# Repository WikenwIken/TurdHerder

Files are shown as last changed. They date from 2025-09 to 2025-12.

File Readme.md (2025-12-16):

# Turd Herder 
## _The Porcelain Standard for 3D Printer Waste Management_
### THIS PROJECT IS A WORK IN PROGRESS.
If you would like to help with the development of this project please join us in the  [Armored Turtle Discord Thread].  The files contained in this github are usable, however unreliable in their current state.

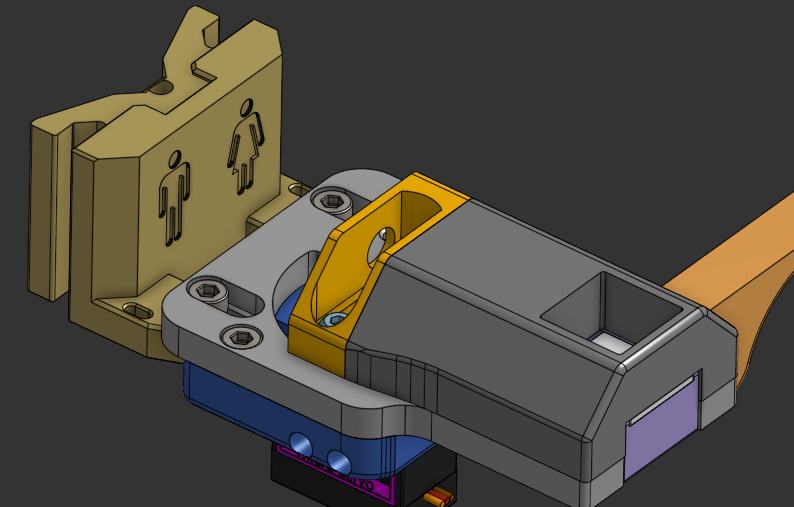
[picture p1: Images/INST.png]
INST


The Turd Herder is a dookie disposal system for 3D printers with toolheads that have limited to no travel past the edges of the print bed.  The bowl extends over the edge of the print bed, receives the "payload," retracts and whisks it off to a tank in the depths below.  

Turd Herder was designed for use with the Voron Trident / Box Turtle AMS combo running Klipper firmware. The macros are designed to integrate with the AFC Macros (included with the Box Turtle system).

The motion system was inspired by [Dendrowen's Blobifier], the mounting system incorporates whole, and modified, parts from [Armored Turtle's AT Brush]  and the macros are modified versions of [ImSundee's Turtleblobifier].

### 2025.11.20 - Added __front_arm_base_extended.stl__ to the 20255.11.01 STL folder and added the corresponding STEP files in an accurate, yet confusingly named folder. 
#### 2025.11.01 - Updated the mounting location of the switch for better reliability and stability.  Only __Cog__, __Slide_Base__ and __Servo_Mount__ have changed since last version. 
##### 2025.09.03 - This project is brand new and only tested by the me so far.  Bugs / hitches are to be expected.  Please report anything that isn't working as expected and it will be addressed. 

## Features

- Can be used with any toolhead / probe combo as there aren't any negative Z moves
- A modified G28 allows for safe Z homing 
- Easy to print parts, no supports required!
- Plugs into a BL Touch Port for easy wiring
- Optional brush attachment creates an all-in-one solution

## Required Tools
- Sodering Iron
- Crimping Tool
- Wire Stripper
- Allen Wrenches / Hex Drivers (1.5, 2, 2.5 and 3 mm)
- Small Phillips Screw Driver

## BOM

| Part | QTY | 
| --- | --- |
| MG90S Servo (180°) + Hardware Kit | 1 |
| Micro Limit Switch (with lever) | 1 |
| Bambu A1 style brush (37x8) | 1 |
| 6 x 3 mm magnet | 2 |
| 15 x 14 x 1 mm aluminum cube | 1 |
| M5 x 10 mm SHCS | 2 |
| M5 Rollnut | 2 |
| M3 Hex Nut | 2 |
| M3 Washer | 1 |
| M3 x 5 x 4 mm Heat Set Insert | 8 |
| M3 x 6 mm SHCS | 2 | 
| M3 x 8 mm SHCS | 4 |
| M3 x 8 mm BHCS | 1 |
| M3 x 6 mm BHCS | 1 |
| M2 x 8 mm SHCS | 2 |
| 3 mm ID Bowden Tube (optional) | ~4.5 mm |
| JST-XH Male / Female Plugs / Crimps | ~ |
| Zip Ties (optional) | ~ |

*Note:  the M3 Hex Nuts MUST be magnetic.  The sled mechanism will not work properly without a strong-ish magnetic connection.*

*Note: The aluminum cube is just a landing pad for the ___hot___ load and can be made of anything that will take the heat better than bare plastic.  We don't want things to stick and get clogged.  I cut up an aluminum plate from an old project box but as long as its <=1mm thick you could fold up some aluminum foil or glue a few layers of soda cans together.  Get creative.*

## Printing

In addition to the STLs in this repositiory, Turd Herder requires the following parts from the [AFC-Accessories] repo.
- [mount_lower.stl]
- [mount_upper.stl]

Parts should be printed in ABS and in accordance to typical Voron specs which may be found [here]. Tolerances for the slots are a little tight and may require some filing to achieve a smooth translation from front to rear.
All parts are oriented correctly and don't require any modifiers from the slicer.  
Supports should not be needed.

# Software Installation
__It is important that the software be installed prior to building the Turd Herder as some of the macros are vital to the assembly process.__

__It is recommended that you make a backup of your __printer.cfg__ and __/AFC/AFC.cfg__ files before proceeding.__

Variables do not need to be tuned at this point, we're just installing the software so the servo macros may be utilized for the build.  We will cover the critical variables later in this document.

1) Clone this project into your printer's config folder ``` git clone https://github.com/WikenwIken/TurdHerder ~/printer_data/config/TurdHerder ```
2) Open TurdHerder/turd_hw.cfg and set the correct values for `pin` and `switch_pin`  
3) Make the following changes to your printer.cfg file:
    - Add ```[include TurdHerder/turdherder.cfg]```
    - Paste the sections `[force_move]` and `[homing_override]` from /turdherder/printurd.cfg into your printer.cfg, adding in any custom features that were previously executed in `[safe_z_home]`
    - Comment out ```[safe_z_home]``` and all lines included within.  This seems crazy but '[homing_override]' and '[safe_z_home]' are incompatable.  
4) Make the adjustments to your /AFC/AFC.cfg file as noted in the second half of the /TurdHerder/printurd.cfg file

# Assembly

1) Install 6 M3 heat set inserts according to Figures 1 and 2: 
    - front_arm_base x2 
    - servo_base x2 
    - chimney x2

Fig. 1    
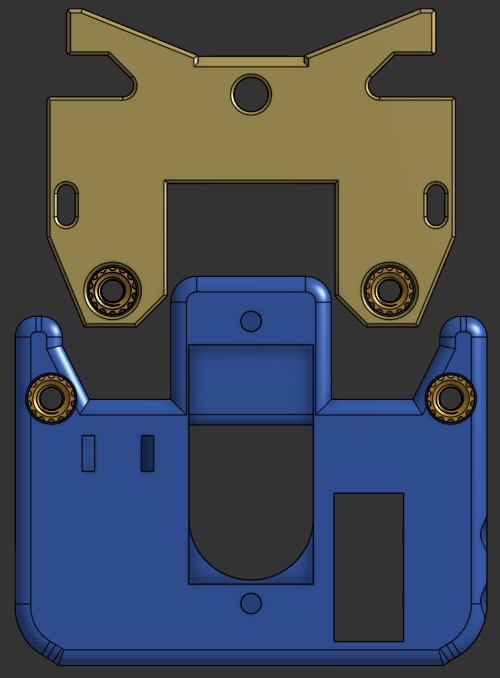
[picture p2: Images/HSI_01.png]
HSI_01


Fig. 2
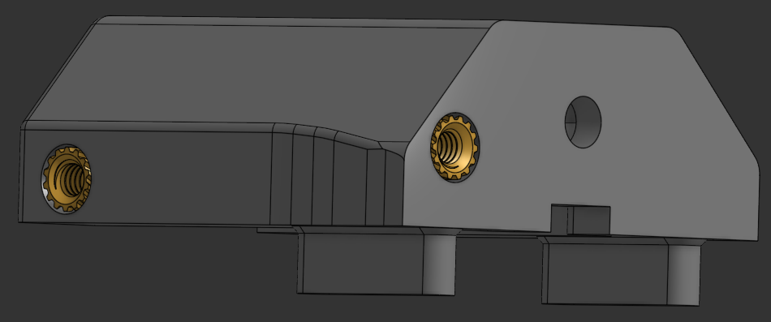
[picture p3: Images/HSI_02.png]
HSI_02


2) Install 2 M3 heat set inserts into __mount_upper__ according to [Step 4] of the AT Brush Manual.
3) Solder one wire to each of the outer pins of the micro limit switch.  Terminate each wire with an appropriate sized crimp / plug.  Orientation in the plug does not matter for the limit switch.
4) MG90S Servos typically ship with dupont connectors.  These will need to be removed and replaced by an appropriate connector.  Consult your main board's pinout diagram before building your new connector.
5) Attach the servo to the __servo_mount__ using the self-tapping screws that came with the servo.  It will only fit one way.
6) Secure the __slide_base__ to the __servo_mount__ using 2 M3x8 SHCS (Figure 3)
7) Plug the servo into the socket on the main board that you defined in /TurdHerder/turd_hw.cfg.  
    - Execute the macro ```SERVO_IN```.  This should rotate the shaft *clockwise*  
    - Execute the macro ```SERVO_OUT```.  This should rotate the shaft *counter-clockwise*
    - If the shaft does not rotate, check your wiring / pin definitions.
    - If the shaft rotates in the wrong direction some modification of the code is likely in order to make it work with your motor.
8) _Make absolutely sure, before proceeding, that your printer homes as expected without the Turd Herder in place._  Run the 'servo_out' macro.  Z should increase and the servo should move after.  Homing the printer should home X and Y first, retract the servo and then move to the "safe" spot and then home Z.
9) Execute the macro ```SERVO_OUT``` and press the __cog__ onto the shaft as seen in Figure 3.  Add the M3 Washer and M2.5 mounting screw if the __cog__ isn't as rigid as you would prefer.  It should be a pretty tight fit.  Once installed, execute the macros ```SERVO_IN``` and ```SERVO_OUT``` to confirm the cog has full range of travel.  
*Note: The motor should complete its move without physically butting up against the frame.  If the motor doesn't stop freely then some physical / code adjustments should be made.*

Fig. 3

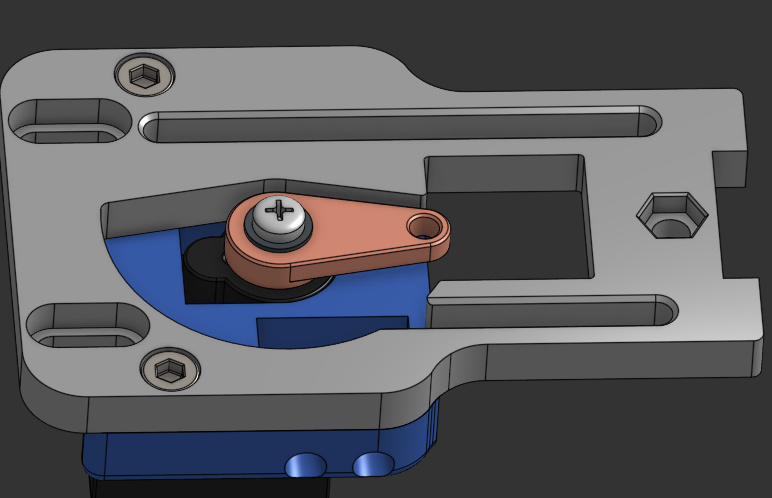
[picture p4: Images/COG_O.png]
COG_O


10) Ensure that the cog is in the position indicated in Figure 3 by running the ```SERVO_OUT``` macro and unplug the servo from the main board before moving on.
11) Feed the limit switch up through the rectangular hole in the __servo_mount__ and secure it in place with M2x8 screws.  __Mind the orientation in Figure 4.__

Fig. 4

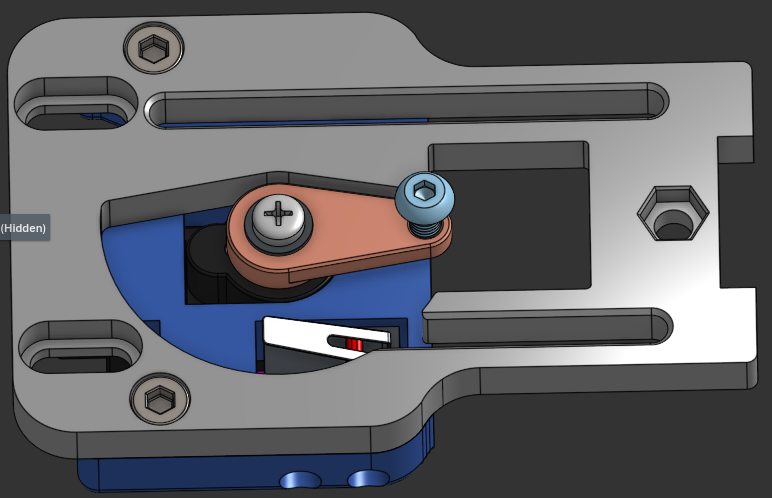
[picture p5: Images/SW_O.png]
SW


12) Insert 1 M3 Hex Nut into the cutout in the __slide_mount__.  If the fit is too tight to press in with your fingers it may be useful to "pull" it into place with an M3 screw from the bottom of the part.  If the fit is too loose use a dab of super glue or insert an M3x4 or M3x5 screw from below that won't protrude above the nut to hold it in place.  
13) Insert 2 6 x 3 mm magnets into the holes in __sled__.  A dab of super glue may be required to old them in place.  Polarity is not important.  Be careful not to split the layers.    
14) Glue the Aluminum Plate onto the tray of the __sled__.  It should not protrude above the edges of the tray.
15) Click the __sled__ in place on the __slide_mount__ (Figure 5)

Fig. 5

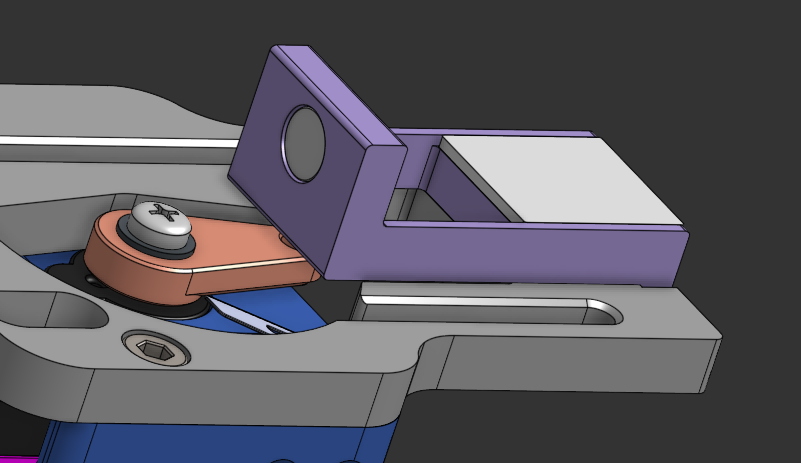
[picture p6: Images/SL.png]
SL


16) Attach the __chimney_slot__ to the __chimney__ by inserting an M3x6 SHCS into the hole on the left-rear of the parts. (Figure 6)
17) Insert 1 M3 Hex Nut into the cutout in the __chimney__ and secure it with an M3x6 BHCS through the holes in the middle. (Figure 7)

Fig. 6

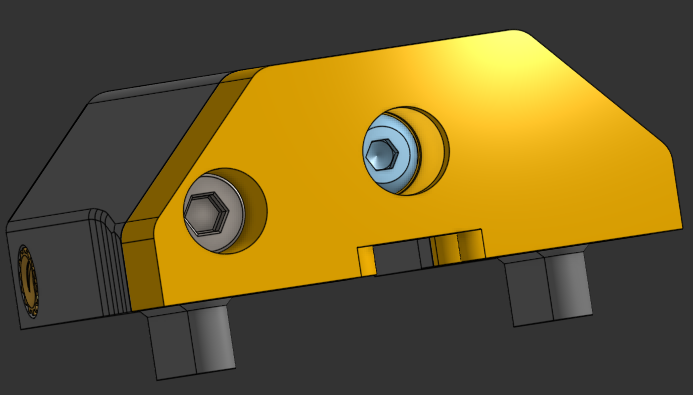
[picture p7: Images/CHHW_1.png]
CHHW_1


Fig. 7

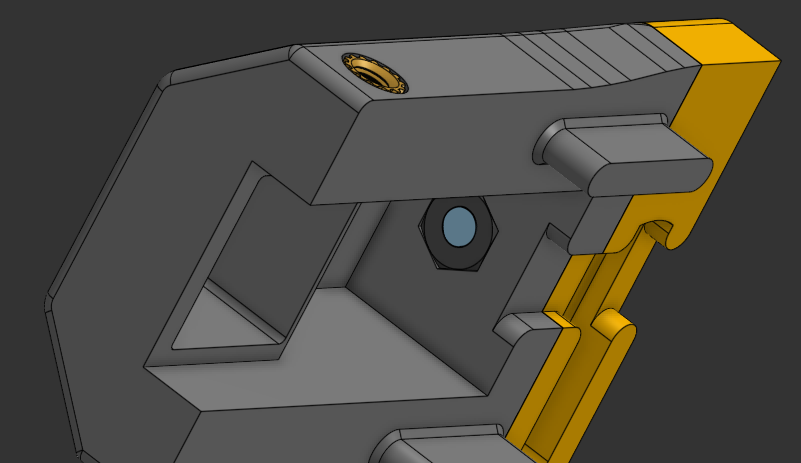
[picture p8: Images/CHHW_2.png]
CHWW_2


18) Drop the chimney assembly into the slots on the __slide_mount__.  The top of the __sled__ inserts into the space in the __chimney__ with the M3 Hex Nut.  Align the slot in the __chimney_slot__ with the hole in the slender end of the __cog__ and screw an M3x8 BHCS into the __cog__ until it is flush with the underside (Figure 8).  It should not protrude from the bottom at all.  This connection should remain fairly loose to allow for free translation of the screw in the slot.  It is easily adjusted later if movement is labored.
_OPTIONAL: A 4mm OD x 3mm ID bowden tube sleeve may be installed around the M3x8 screw to cut down on the threads wearing out the slot_

Fig. 8

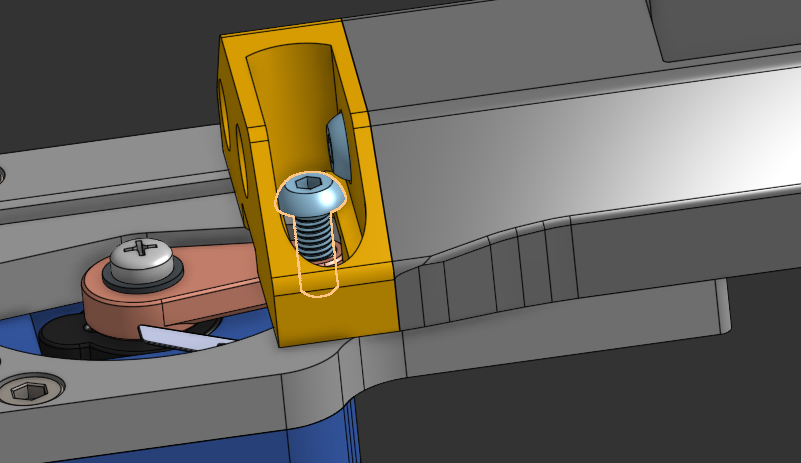
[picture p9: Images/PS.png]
PS


19) Attach the __brush_arm__ to the __chimney__ using an M3x6 SHCS (Figure 9).

Fig. 9

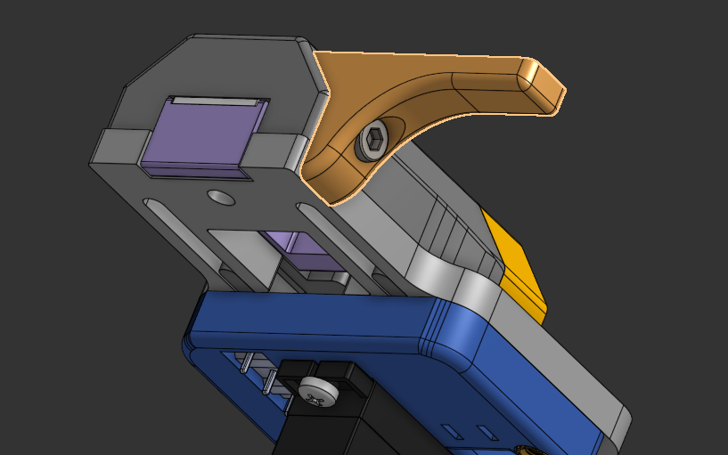
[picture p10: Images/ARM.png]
ARM


20) Attach the silicone brush to the top surface of the __brush_arm__ 
21) Assembly of the Turd Herder is complete.  (Figure 9)

22) Follow these instructions in the [AT Brush Manual] utilizing the modified __front_arm_base__ from this repository:
    - Steps 1 - 8
    - Steps 13 - 15
23) Loosely attach the Turd Herder assembly to the frame mount assembly using 2 M3x8 SHCS (Figure 9).  Adjust the Y positioning so that there is ~1-2mm gap between the front of the Turd Herder and the print bed and tighten the screws.

Fig. 9

INST

24) Adjust the height of the assembly so that, when the Turd Herder is extended, the nozzle comes in contact with the brush on the Z axis.  (See Step 16 in the [AT Brush Manual])

25) Plug the servo and the limit switch into the main board.  
    - Ensure smooth movement by cycling through the `SERVO_IN`, `SERVO_MID` and `SERVO_OUT` macros
    - Ensure the `turdherd` limit switch reads *detected* in the `SERVO_IN` and `SERVO_MID` positions.
    - Ensure the `turdherd` limit switch reads *not detected* in the `SERVO_OUT` position.
26) Congratulations!  The Turd Herder is fully assembled and the mechanism is working as intended!  Don't release those bowels just yet, there are a few more things to set up.

# Critical Variables
The following are the _must have_ variables that need to be defined for the specific printer that Turd Herder is being installed in.  Each variable is accompanied with a description within the .cfg file.
## turd_hw.cfg 
`[servo TURDHERDER]`
* `pin`

`[filament_switch_sensor turdherd]`
* `switch_pin`

## turdherder.cfg
`[gcode_macro TURDHERDER]`
* `variable_purge_spd`
* `variable_thbottom`
* `variable_brush_start_x`
* `variable_brush_start_y`
* `variable_purge_x`
* `variable_purge_y`
* `variable_tray_angle_mid`

## printer.cfg / printurd.cfg
`[homing_override]`
* `home_pos_x`
* `home_pos_y`

   [Dendrowen's Blobifier]: <https://github.com/Dendrowen/Blobifier>
   [ImSundee's Turtleblobifier]: https://github.com/ImSundee/Turtleblobifier
   [Armored Turtle's AT Brush]: https://github.com/ArmoredTurtle/AFC-Accessories/tree/main/AT_Brush
   [AFC-Accessories]: https://github.com/ArmoredTurtle/AFC-Accessories
   [mount_lower.stl]: https://github.com/ArmoredTurtle/AFC-Accessories/blob/main/AT_Brush/STLs/mount_lower.stl
   [mount_upper.stl]: https://github.com/ArmoredTurtle/AFC-Accessories/blob/main/AT_Brush/STLs/mount_upper.stl
   [here]:<https://docs.vorondesign.com/sourcing.html#print-settings>
   [AT Brush Manual]: https://www.armoredturtle.xyz/manual.html?manual=at_brush&step=1
   [Step 4]: https://www.armoredturtle.xyz/manual.html?manual=at_brush&step=4
   [Armored Turtle Discord Thread]: https://discordapp.com/channels/1229586267671629945/1413552213695008869

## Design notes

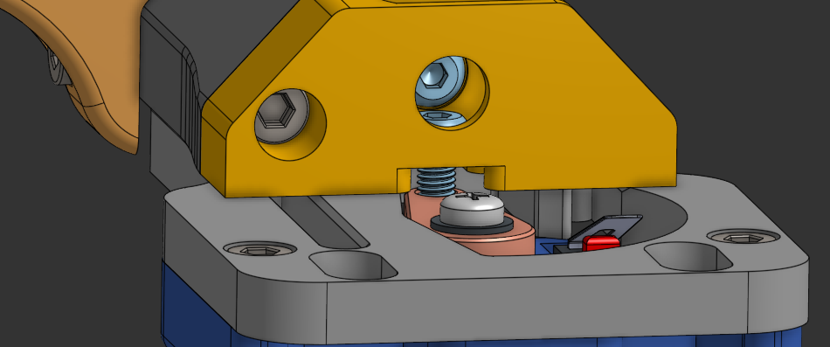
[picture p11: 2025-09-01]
Images/Hardware.png

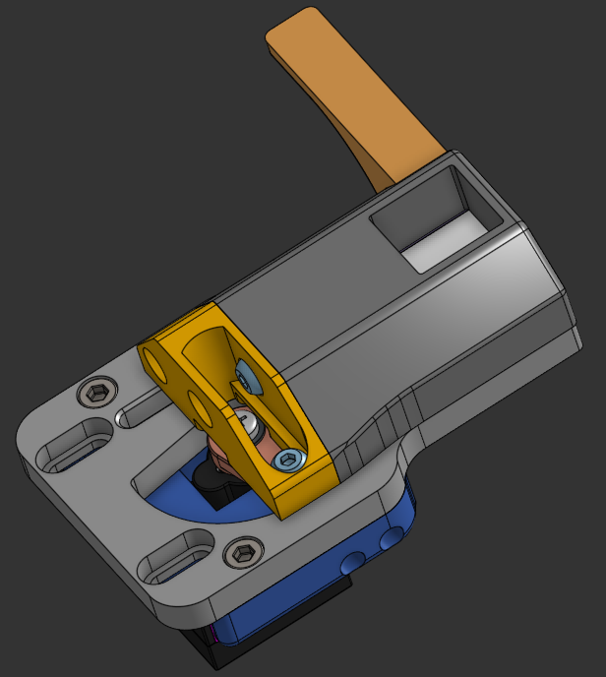
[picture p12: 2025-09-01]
Images/FINAL.png

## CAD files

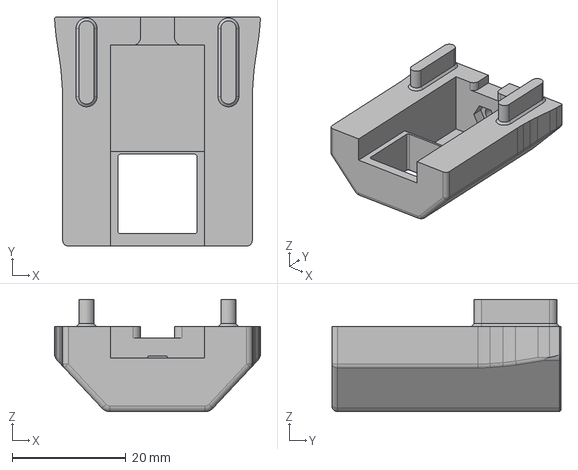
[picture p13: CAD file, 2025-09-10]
2025.09.09.Turd Herder_STEP/Chimney.step
36.3 x 40.4 x 19.8 mm

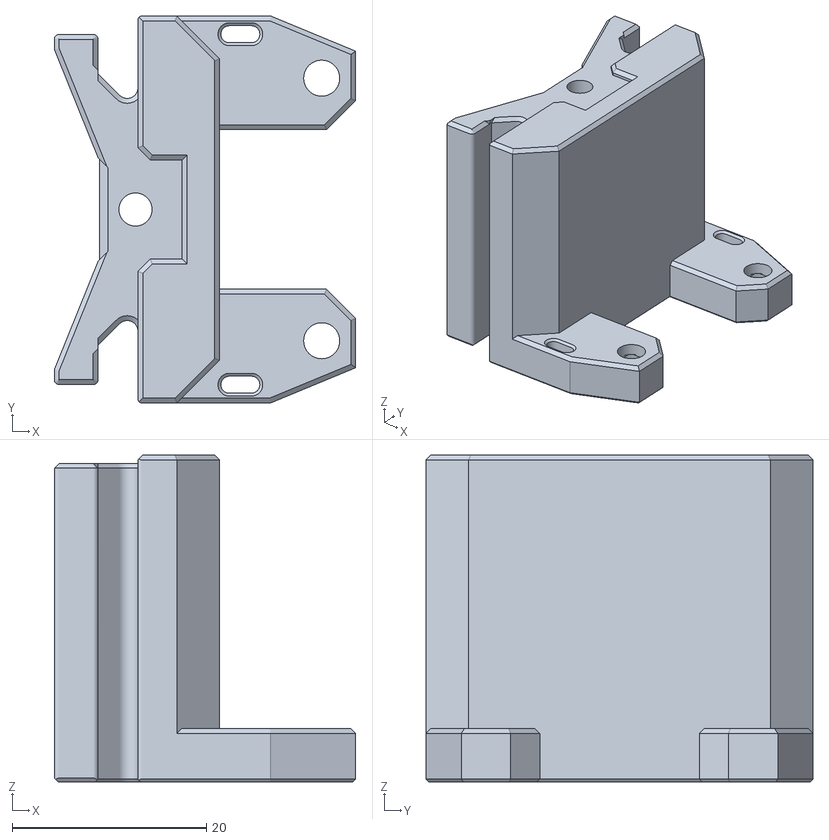
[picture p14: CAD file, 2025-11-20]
2025.11.01_Turd_Herder_STL/front_arm_base_taller.stl
31.0 x 39.8 x 33.6

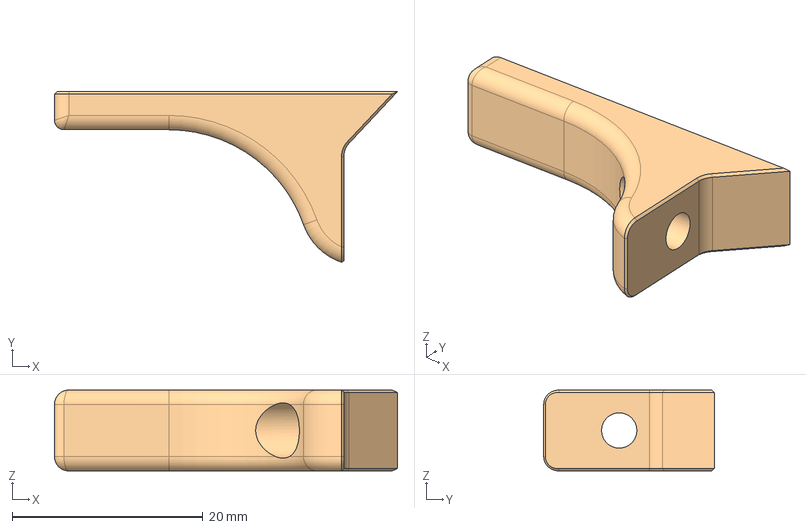
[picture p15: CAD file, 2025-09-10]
2025.09.09.Turd Herder_STEP/Brush_Arm.step
36.0 x 17.9 x 8.50 mm

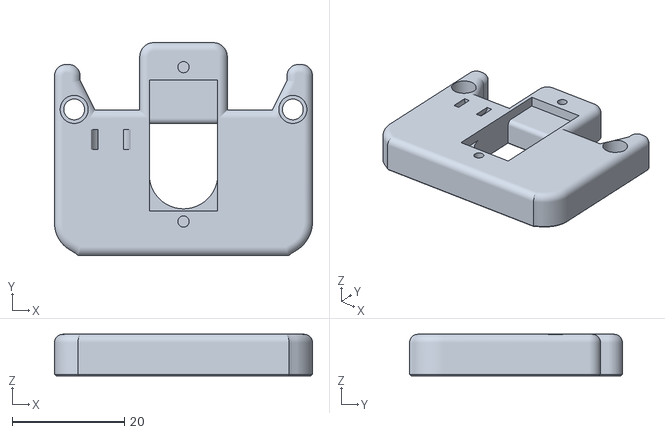
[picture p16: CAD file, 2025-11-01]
2025.11.01_Turd_Herder_STL/Servo_Mount.stl
46.0 x 37.9 x 7.40

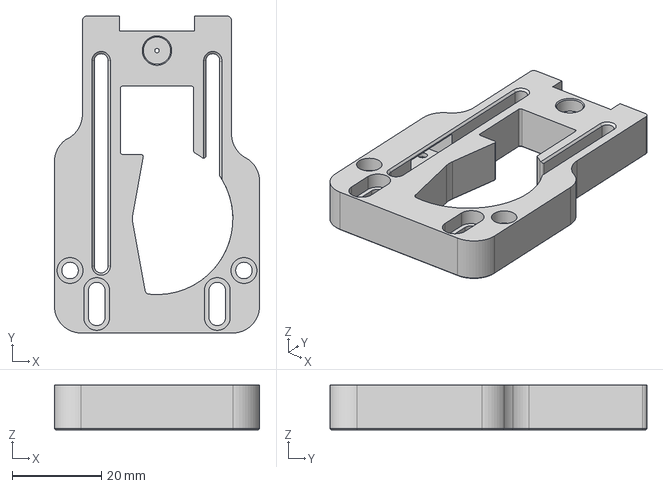
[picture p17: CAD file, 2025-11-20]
2025.11.20_Side_Switch_Parts_STEP/Side_Switch - Slide_Base.step
45.9 x 71.0 x 10.0 mm

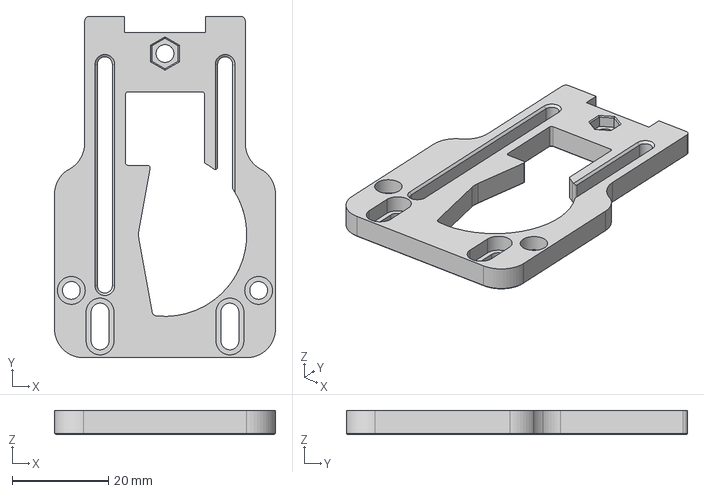
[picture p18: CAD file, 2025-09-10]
2025.09.09.Turd Herder_STEP/Slide_Base.step
45.9 x 71.0 x 5.00 mm

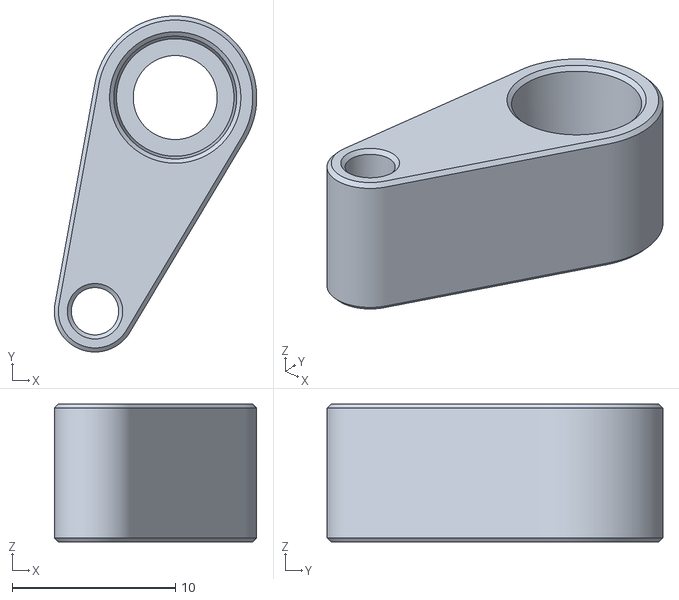
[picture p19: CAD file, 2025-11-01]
2025.11.01_Turd_Herder_STL/Cog.stl
12.4 x 20.6 x 8.45

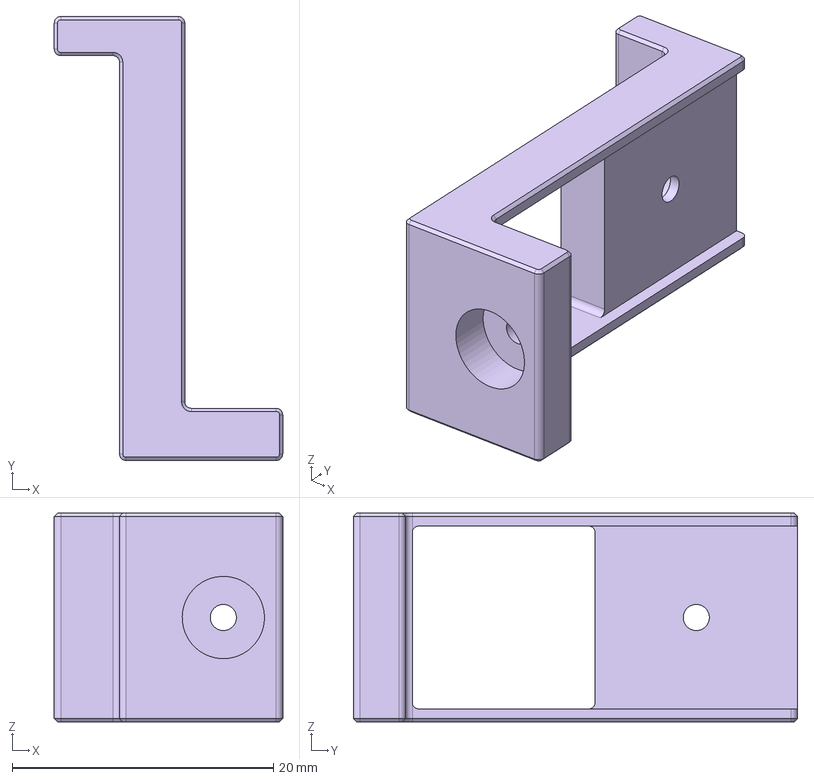
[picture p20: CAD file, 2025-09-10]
2025.09.09.Turd Herder_STEP/Sled.step
17.5 x 34.0 x 16.0 mm

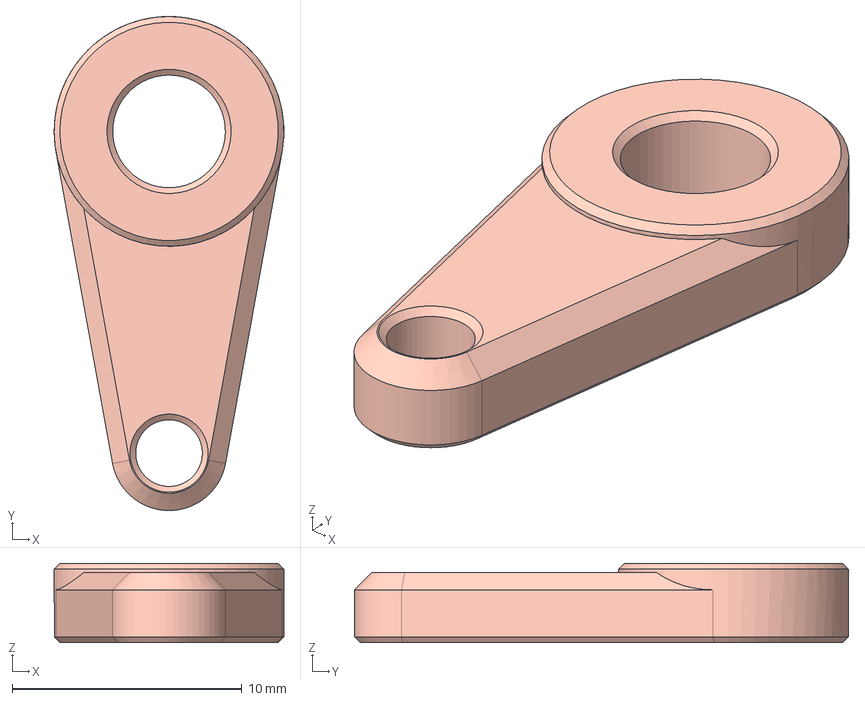
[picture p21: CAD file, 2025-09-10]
2025.09.09.Turd Herder_STEP/Cog.step
9.99 x 21.5 x 3.45 mm

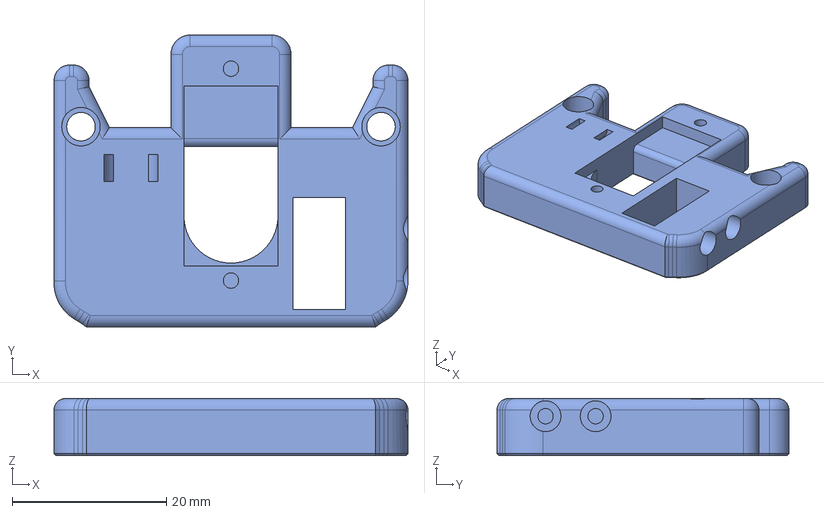
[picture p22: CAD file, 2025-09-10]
2025.09.09.Turd Herder_STEP/Servo_Mount.step
45.9 x 37.9 x 7.40 mm

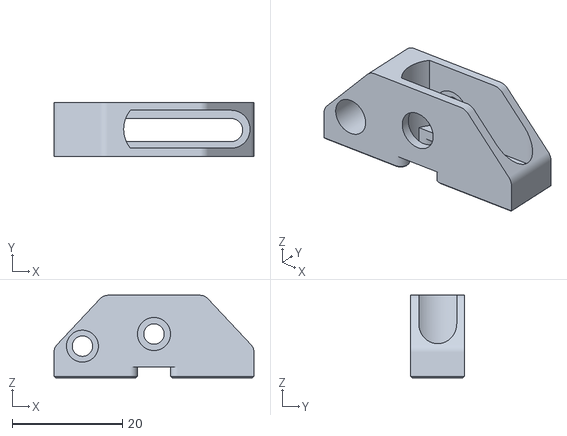
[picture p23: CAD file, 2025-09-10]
2025.11.01_Turd_Herder_STL/Chimney_Slot.stl
36.3 x 9.80 x 15.0

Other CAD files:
2025.11.20_Side_Switch_Parts_STEP/front_arm_base_taller.step
2025.11.20_Side_Switch_Parts_STEP/Side_Switch - Cog.step
2025.11.01_Turd_Herder_STL/Slide_Base.stl
2025.11.20_Side_Switch_Parts_STEP/Side_Switch - Servo_Mount.step
2025.11.01_Turd_Herder_STL/Chimney.stl
2025.09.09.Turd Herder_STEP/Chimney_Slot.step
2025.11.01_Turd_Herder_STL/Brush_Arm.stl
2025.09.09.Turd Herder_STEP/Front_Arm_Base.step
2025.09.09.Turd Herder_STL/Front_Arm_Base.stl
2025.11.01_Turd_Herder_STL/Sled.stl

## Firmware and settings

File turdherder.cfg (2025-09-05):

# Include servo hardware definition separately to allow for automatic upgrade
[include turd_hw.cfg]

##########################################################################################

# Sample config to be used in conjunction with TURDHERDER.  Created by NightWiken 
# (NightWiken on Discord). The macro is a modified version of Blobifier for AFC by 
# ImSundee.

# IMPORTANT: It is very important to modify your printer.cfg by commenting out the 
# [safe_z_homing] section and replacing it with the [force_move] and [homing_override] 
# sections located printurd.cfg

# The TURDHERDER uses some room at the back-left side of your printer, depending on your
# printer limits and positions. (usually max_pos.y - toolhead_y and brush_start + 
# brush_width + toolhead_x). If you do place objects within this region, TURDHERDER will
# skip purging automatically. It does this by extending the EXCLUDE_OBJECT_* macro's, so
# make sure you have exclude objects enabled in your slicer.

###################################### DISCLAIMER ########################################

# You, and you alone, are responsible for the correct execution of these macros and 
# gcodes. Any damage that may occur to your machine remains your responsibility. 
# Especially when executing this macro for the first few times, keep an eye on your 
# printer and the emergency stop.

# Notes on parameters:
# PURGE_LENGTH=[float] (optional) The length to purge. If ommited (default) it will check
#                      the purge_volumes matrix or variable_purge_length. This can be used
#                      to override and for testing.

[gcode_macro TURDHERDER]
# These parameters define your filament purging.
# Note that the control of retraction is set in 'mmu_macro_vars.cfg' which can be increased
# if you experience excessive oozing.
variable_purge_spd: 480                 # Speed, in mm/min, of the purge.
variable_purge_temp_min: 200            # Minimum nozzle purge temperature.
variable_toolhead_x: 70                 # From the nozzle to the left of your toolhead
variable_toolhead_y: 50                 # From the nozzle to the front of your toolhead

variable_retract_before_park:    3.0     # amount in mm. 0 to disable
variable_retract_speed:       2000       # mm/m
variable_retracted_length:  0.4	# Amount of current retraction

# This macro will prevent a gcode movement downward while 'blobbing' if there might be a
# print in the way (e.g. You print something large and need the area where TURDHERDER does
# its... 'business'). However, at low heights (or at print start) this might not be
# desireable. You can force a 'safe descend' with this variable. Keep in mind that the 
# height of the print is an estimation based on previous heights and certain assumptions
# so it might be wise to include a safety margin of 0.2mm
variable_force_safe_descend_height_until: 1.0 

# Adjust this so that your build plate is just lower than the bottom of the Turd Herder.  
# It is recommended to leave at least 2 mm of space.
# This will also be the maximum Z height that requires a Z move during the purge sequence.
variable_thbottom: 23

# These parameters define your scrubbing, travel speeds, safe z clearance and how many
# times you want to wipe. Update as necessary.
variable_wipe_qty:              4          # Number of complete (A complete wipe: left,
                                           #   right, left OR right, left, right) wipes.
variable_travel_spd_xy:      25000          # Travel (not cleaning) speed along x and
                                           #   y-axis in mm/min.
variable_travel_spd_z:       2000          # Travel (not cleaning) speed along z axis
                                           #   in mm/min.
variable_wipe_spd_xy: 30000          # Nozzle wipe speed in mm/min.

# The acceleration to use when using the brush action. If set to 0, it uses the already 
# set acceleration. However, in some cases this is not desirable for the last motion 
# could be an 'outer contour' acceleration which is usually lower.
variable_brush_accel: 10000

# If you have skew correction enabled and get 'move out of range' errors 
# regarding TURDHERDER while skew is enabled, try increasing this value. Keep the 
# adjustments small though! (0.1mm - 0.5mm) and increase it until it works.

variable_skew_correction: 0.1

# These parameters define the size of the brush. Update as necessary. A visual reference
# is provided below.
#
#                     ←   brush_width   →
#                      _________________
#                     |                 |  ↑                Y position is acquired from your
#  brush_start (x, y) |                 | brush_depth       stepper_y position_max. Adjust
#                     |_________________|  ↓                your brush physically in Y so
#                                                           that the nozzle scrubs within the
#                                                           brush.
# __________________________________________________________
#                        PRINTER FRONT


# Set the start location of the brush. Extend the Turd Herder using the SERVO_OUT command.
# Position the print nozzle at the left side of the brush and input the X and Y coordinates below.
variable_brush_start_x:           74.0  
variable_brush_start_y:           295.0

# width of the brush
variable_brush_width: 35

# Set location of where to purge. Extend the Turd Herder using the SERVO_OUT command.
# Position the print nozzle at the center of the "bowl" and input the X and Y coordinates below.
variable_purge_x: 61.0
variable_purge_y: 300.0

# Servo angles for tray positions.  tray_angle_mid should be adjusted so that the limit switch
# "turdherd" is detected when in this position.  Utilize the following command in the console
# to dial in the position: SET_SERVO SERVO=TURDHERDER ANGLE={angle}
# Odds are, if this needs adjusting, the angle needs is too high.  Decrease the angle by 5-10°
# until the switch is triggered every time SERVO_MID is called.
# tray_angle_out / _in should only require adjustment if the cog is bottoming out against the 
# frame.
variable_tray_angle_out: 180
variable_tray_angle_mid: 90
variable_tray_angle_in: 0

# ========================================================================================
# ==================== BLOB TUNING =======================================================
# ========================================================================================

##########################################################################################
# The following comment block about purge variables is left in from the original Blobifier
# code in the hopes that someone more intelligent than I might be able to optimize the 
# purge without the assist of the Z move. -NightWiken
##########################################################################################
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

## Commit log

2025-08-13 Original Upload
    [turd_hw.cfg, turd_vars.cfg, turdherder.cfg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]
2025-09-02 Initial Upload of Files
    Original Code Release
    [printurd.cfg, turd_hw.cfg, turdherder.cfg]
2025-09-05 Update turdherder.cfg
    Added verbage for adjusting servo angles
    [turdherder.cfg]
2025-09-05 Update turdherder.cfg
    Added verbage for tuning servo angles
    [turdherder.cfg]
2025-09-10 Added chamfer to bottom surfaces
    Added a 0.25mm chamfer to bottom surfaces of all models to help combat elephants foot.
    [Brush_Arm.step, Brush_Arm.stl, Chimney.step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]
2025-11-01 Changed switch mount
    Moved switch mounting to the side for smoother travel.
    [Brush_Arm.stl, Chimney.stl, Chimney_Slot.stl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]
2025-11-20 Add files via upload
    Only these parts changed in this version.
    [Side_Switch - Cog.step, Side_Switch - Servo_Mount.step, Side_Switch - Slide_Base.step]
